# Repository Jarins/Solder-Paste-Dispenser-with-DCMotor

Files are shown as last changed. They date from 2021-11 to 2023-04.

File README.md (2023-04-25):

# 3D Printed Solder-Paste-Dispenser with DC motor
Motorized automatic solder paste dispenser. Easily printable on a 3D printer at home
+ **Thanks [kevarek](https://hackaday.io/Kevarek) for inspiration from this [project:](https://hackaday.io/project/169748-low-cost-solder-paste-dispenser)**
+ The idea came from this project, including some parts of the source code that were partially or completely reworked and many new ones added. 

## __Work-in-progress__ Latest version 2.21.11.3010

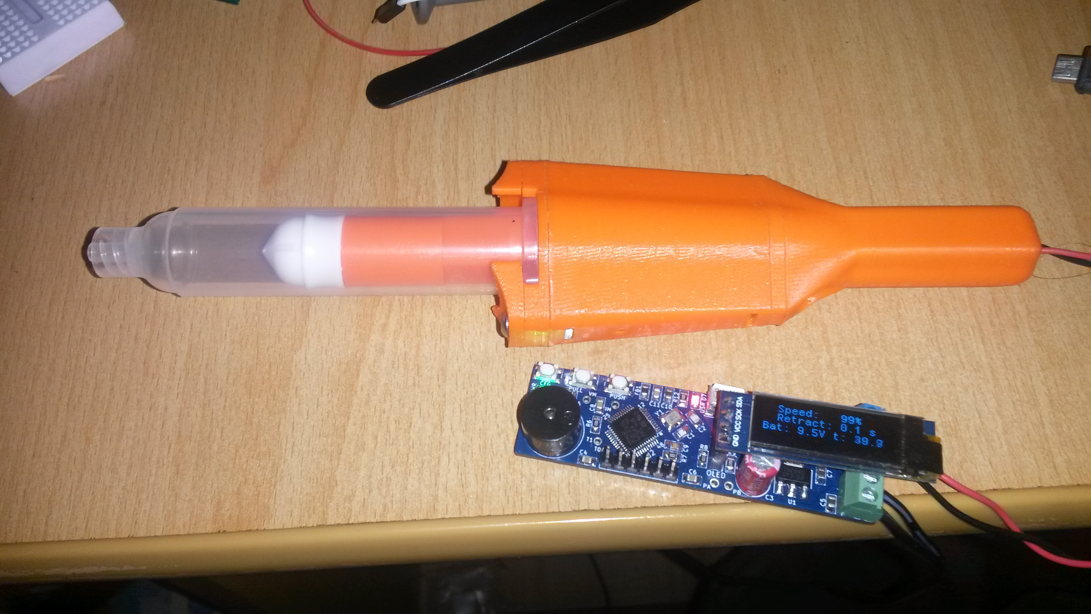
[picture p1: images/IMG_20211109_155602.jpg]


### Some differences:

+ Controled with 32bit processor STM32F103C8T6 ( original is STM32F030)
+ used output H-bridge for motor control [TB67H451FNG](https://www.aliexpress.com/item/1005001738294266.html?spm=a2g0s.9042311.0.0.27424c4dVMVyey). **No need cooling with during operation**.
+ 
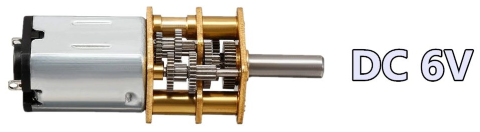
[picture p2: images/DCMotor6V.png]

+ [DC micromotor 6V / 60 rpm](https://www.aliexpress.com/item/33022320164.html?spm=a2g0s.9042311.0.0.266b4c4dmW3uVV) with gearbox without thread rod 


+ [Coupler](https://www.aliexpress.com/item/1005002015620915.html?spm=a2g0s.9042311.0.0.266b4c4dmW3uVV) 3/4mm to thread rod M4.
 
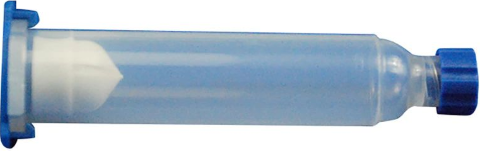
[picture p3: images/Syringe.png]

+ larger [syringe 10 ccm](https://www.aliexpress.com/item/10000092421369.html?spm=a2g0s.9042311.0.0.27424c4dw27aah)

+ **redesigned mechanism of operation and piston mounting and mainly redesigned Syringe mount, which can be removed and put on without disassembling the dispenser**

!! warning component links may be invalid over time !!

----------------------------------------------------------------------

+ [I2C OLED display 128x32](https://www.aliexpress.com/item/32879702750.html?spm=a2g0s.9042311.0.0.27424c4d1LUqwi) pixels for setting dispensing parameters and monitoring operating data
+ The supply voltage is 9V
+ The MicroUSB port is only used for 5V power supply when programming and debugging firmware to save battery. In this mode it is necessary to disconnect the 9V battery. The USB DM and DP pins are connected to the CPU, but the firmware does not respond to them. 
+ **Resistor R2** (in schematic) for measuring motor current is in the current version mounted with the value 0R, because the possibility of measuring this current is not used at the moment. When this value (0R) is used, the H-bridge turns off motor current monitoring.

#### PCB is designed by KiCAD software
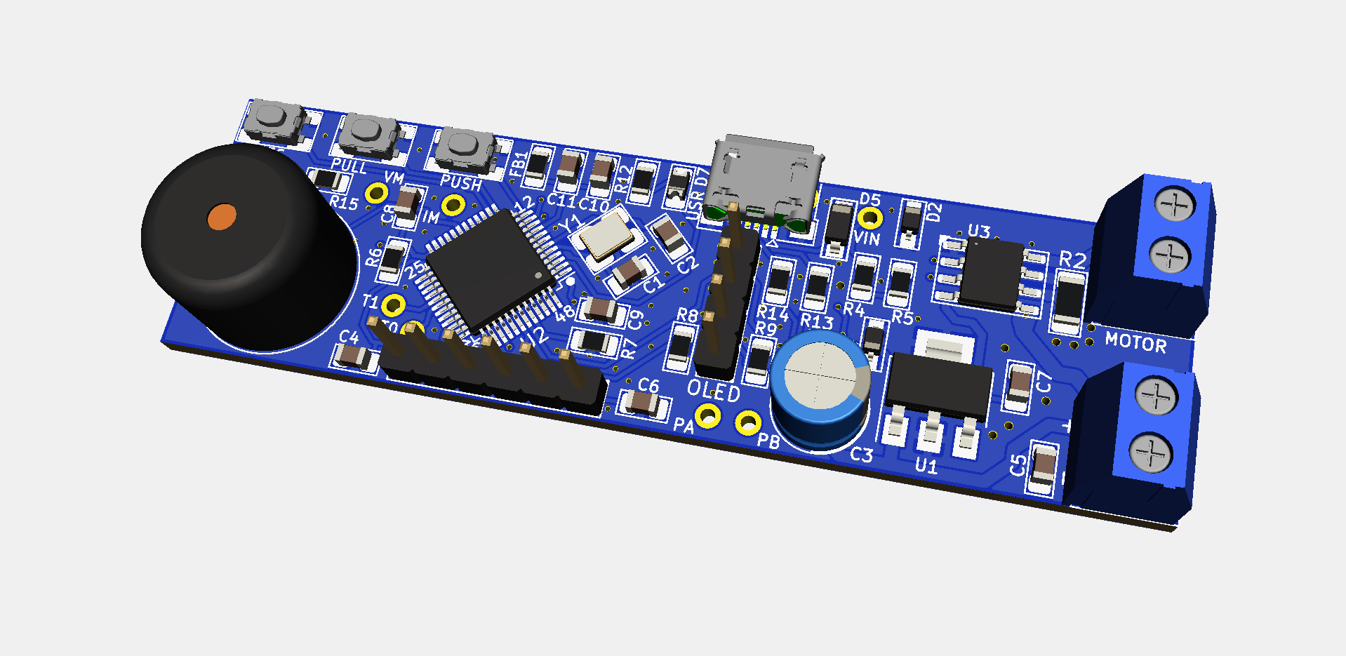
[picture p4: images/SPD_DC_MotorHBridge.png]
Pict2


+ Source code of Firmware is optimized for STM32CubeIDE and CubeMX software from ST Microelectronics.

+ Source code are easy aplicable to another IDE.

+ It would be a little more difficult to migrate to the Arduino IDE, but even that is partially possible - it has not been tested

+ CAD files are designed in SolidWorks, preview [here](https://grabcad.com/library/3d-printed-solder-paste-dispenser-1):

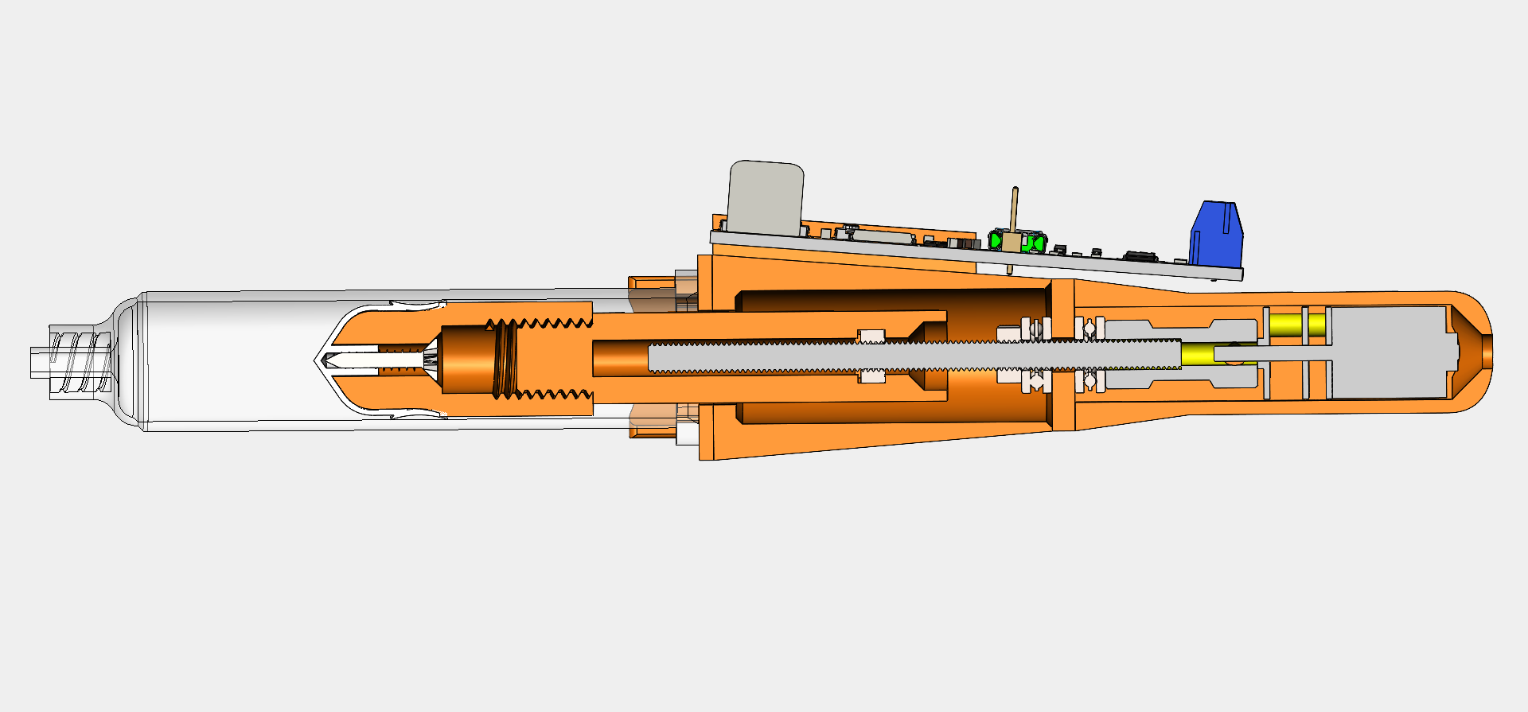
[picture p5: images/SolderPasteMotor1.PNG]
 

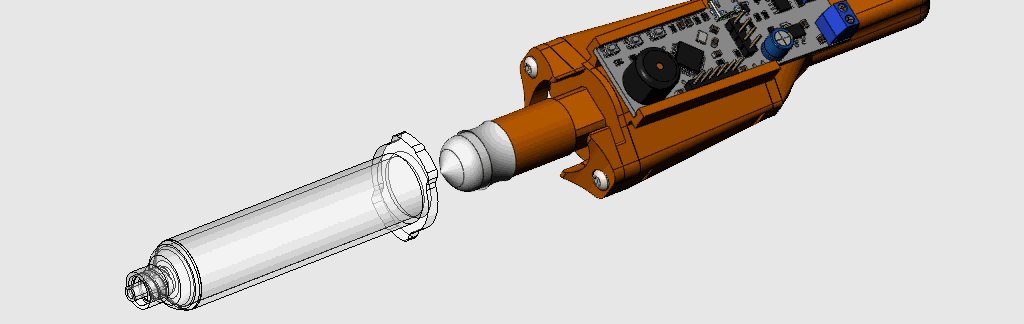
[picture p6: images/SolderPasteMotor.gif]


**Auto Extrusion cycle:**
+ PUSH button short switch ON -> Return from retract(retract duration time) -> Pulse for extrusion(pulse time) -> Retract(retract duration time)

**Manual Extrusion** 
+ PUSH button long switch ON(more as Retract duration time + Pulse time) -> extrusion until the PUSH button is switch OFF. This mode is used to insert a filled Syringe.

**Manual Retract**
+ PULL button switch ON -> retraction until the PULL button is switch OFF. This mode is using for remove and fill Syringe.
+
+ After selection, all parameters are immediately saved in the emulated EPROM (FLASH CPU).
+ Speed: 5, 10, 15 ...... 100% step by 5% 
+ Retract duration: 0(dissable), 100, 200 ...... 2500ms step by 100 milliseconds
+ Pulse after piston returned from retraction: 0(dissable), 100, 200 ..... 1500ms  step by 100 milliseconds 
+ Continuous measurement of battery voltage and CPU temperature
+ The firmware uses a non-blocking I2C DMA routine for the OLED display (this saves about 20 ms in the loop) **and Loop() no waiting to DMA complete as is usual in many of the examples given, which then makes the DMA a blocking wait routine**
+ In addition, non-blocking User Timers derived from SysTick interrupts are used, which do not stop the CPU while waiting for the Timer to run out. The number of these Timers is limited only by the CPU speed and the amount of allocated RAM) *more about this in* [*loop.c*](Software/CubeMX/Application/loop.c)

+ **Tasks**
+ [x] ***The continuation of the work consists in the completion of the control button mounted on the Syringe tube and the tuning of the SW for optimal paste dispensing. This is a game with engine on and off times and duty cycle of PWM wave***
+ [ ] Create a video with instructions for assembly and demonstration at work. Soon.
+ [ ] electronics attachment and power supply solution for the future possibility of 12V power supply from a 3D printer.
+ [ ] Next step is using this solder paste dispenser with a 3D printer. It may be necessary to use a stepping motor for dispensing instead. It has a better and more accurate dispensing control option. I have already finished the PCB for this variant with the DRV8825 controller and the NEMA14 stepper motor. 

UPDATE 11/22/2021:
- Syringe control button completed
- New version firmware 2.0. No blocked Dealy() in Loop() cycle
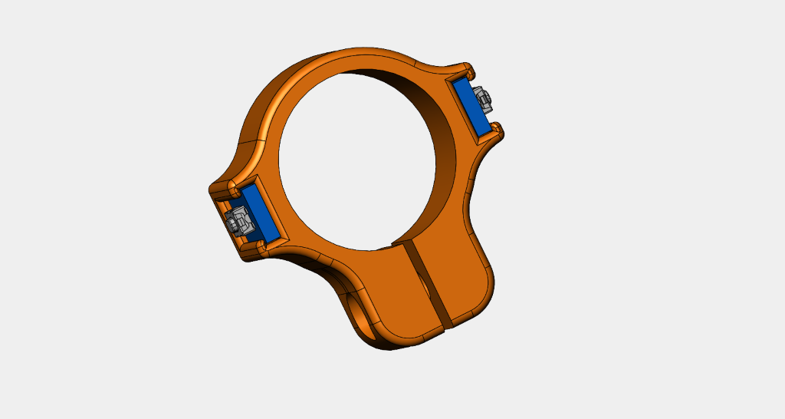
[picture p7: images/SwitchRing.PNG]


#### [Video Assembly and first testing](https://youtu.be/biS96wBTfaU) (redirect to YouTube) 
+ The first version of the printouts on my 3D printer
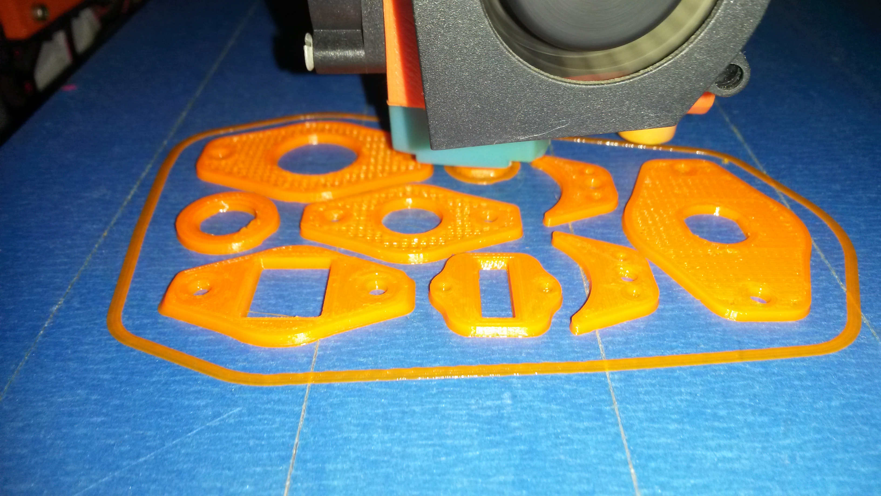
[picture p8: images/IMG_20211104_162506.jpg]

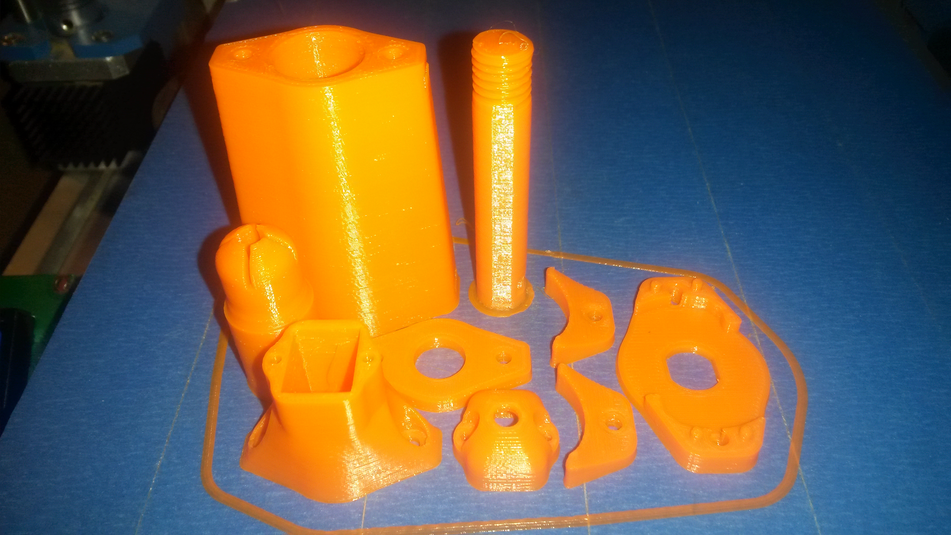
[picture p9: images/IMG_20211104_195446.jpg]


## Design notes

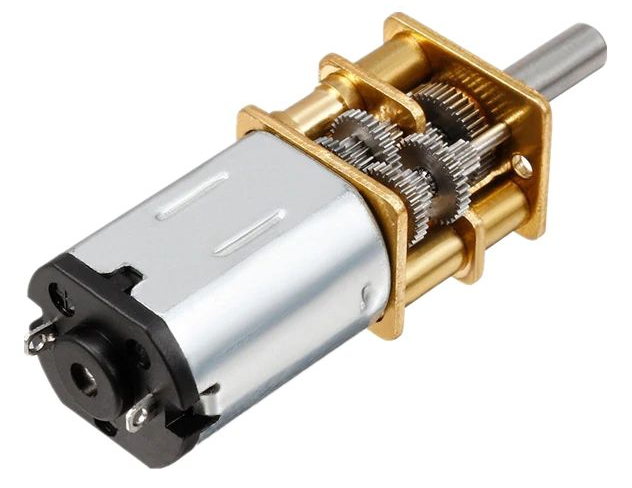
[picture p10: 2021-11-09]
images/DCMotor6V_1.png

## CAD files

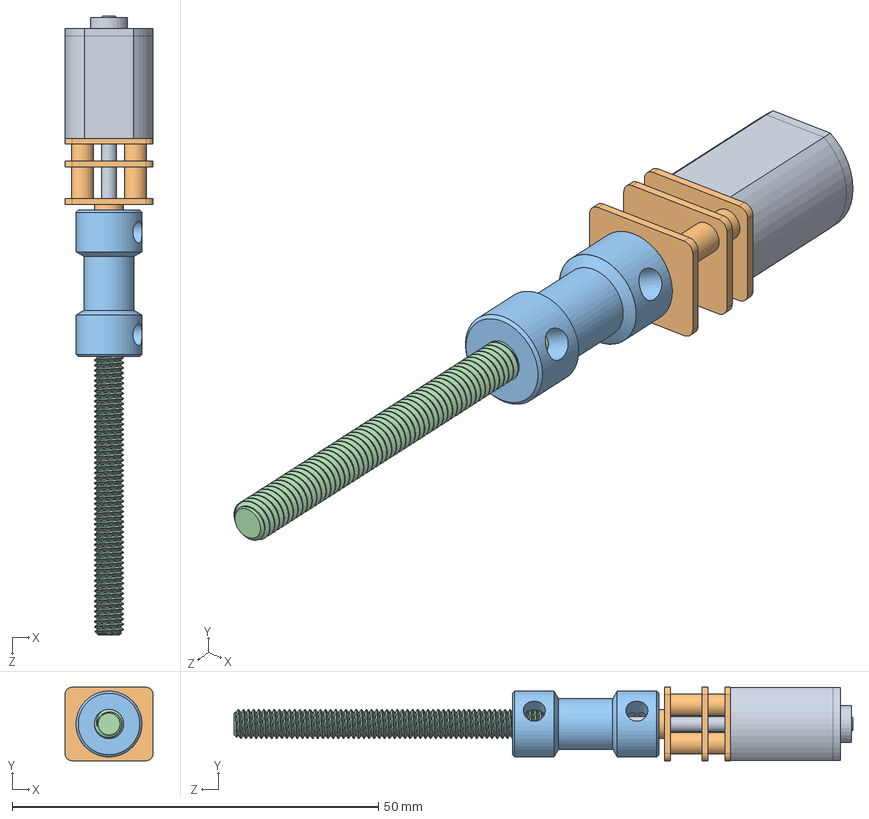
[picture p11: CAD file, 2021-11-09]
CAD/MotorGearBox.SLDASM
12.1 x 10.0 x 84.5 mm
Motor
GearBox
Coupling
ThreadRod

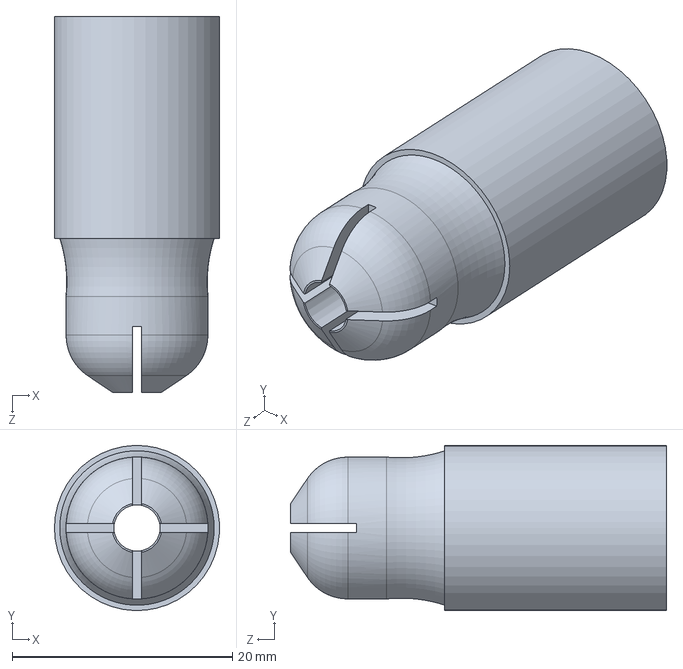
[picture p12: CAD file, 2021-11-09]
CAD/PistonHolder.SLDPRT
15.0 x 15.0 x 34.2 mm

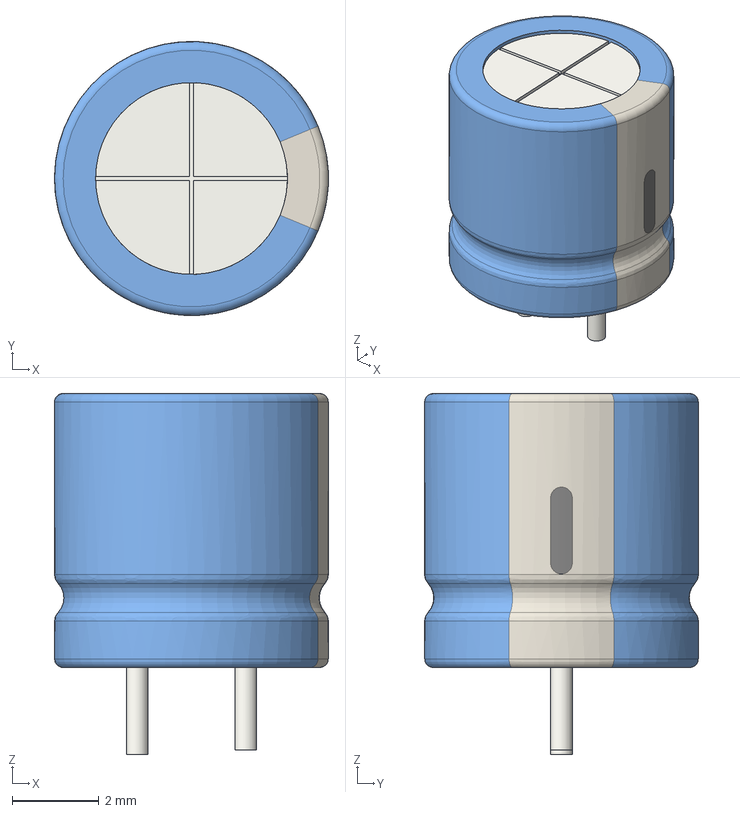
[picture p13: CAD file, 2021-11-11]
Hardware/shapes3D/CP_Radial_D6.3mm_P2.50mm.step
6.30 x 6.30 x 8.30 mm

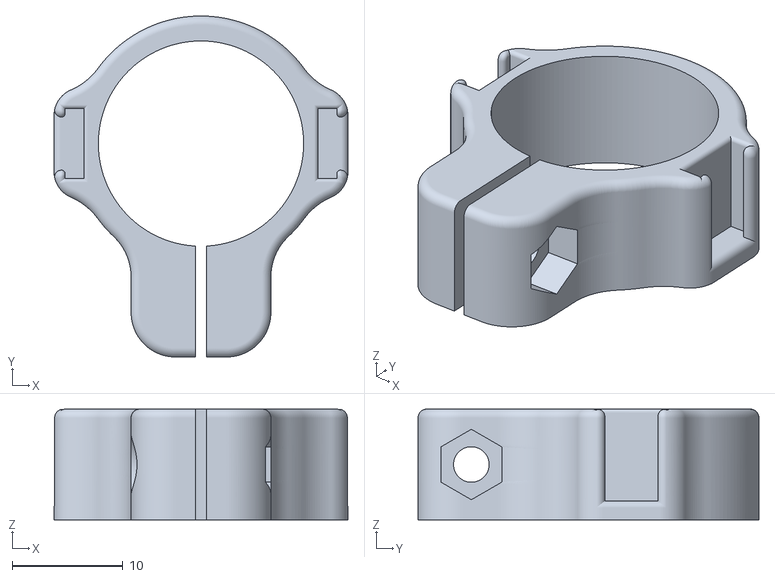
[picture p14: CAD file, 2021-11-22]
STL/SwitchRing.STL
26.5 x 30.7 x 10.0

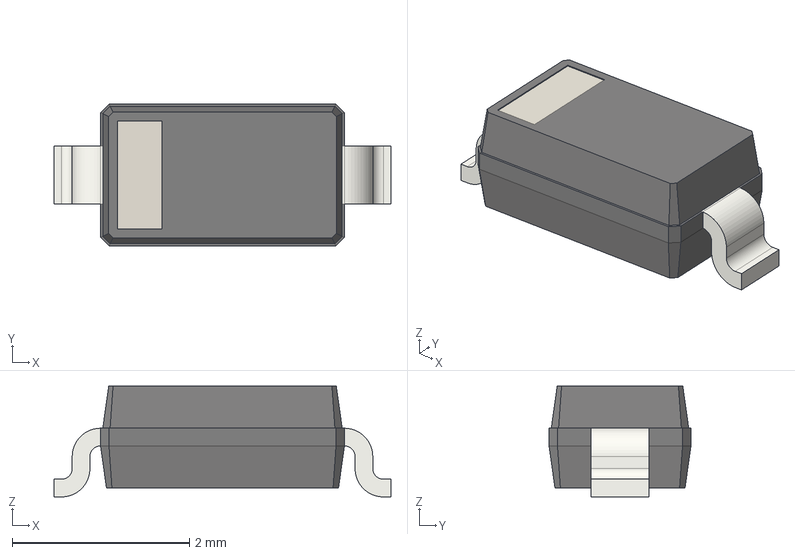
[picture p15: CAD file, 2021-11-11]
Hardware/shapes3D/D_SOD-123.step
3.80 x 1.60 x 1.25 mm

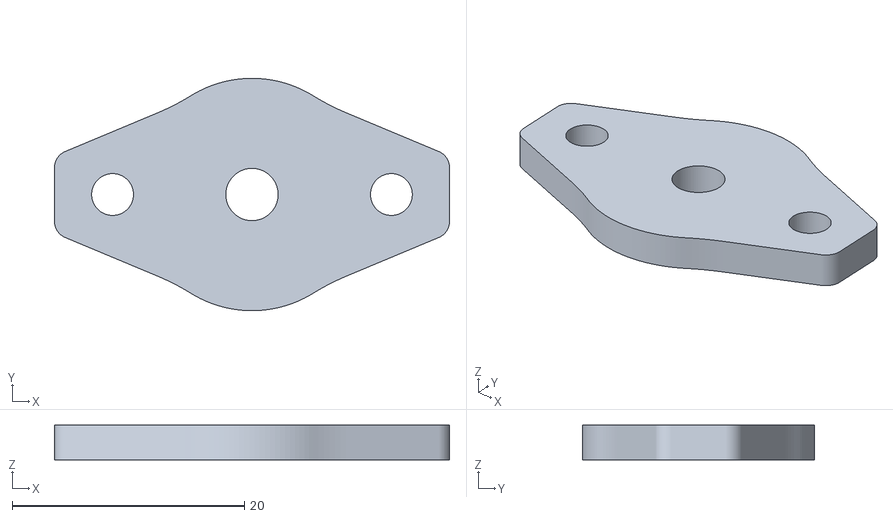
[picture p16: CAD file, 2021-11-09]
STL/ShaftMountFlatAxial.STL
34.0 x 20.0 x 3.00

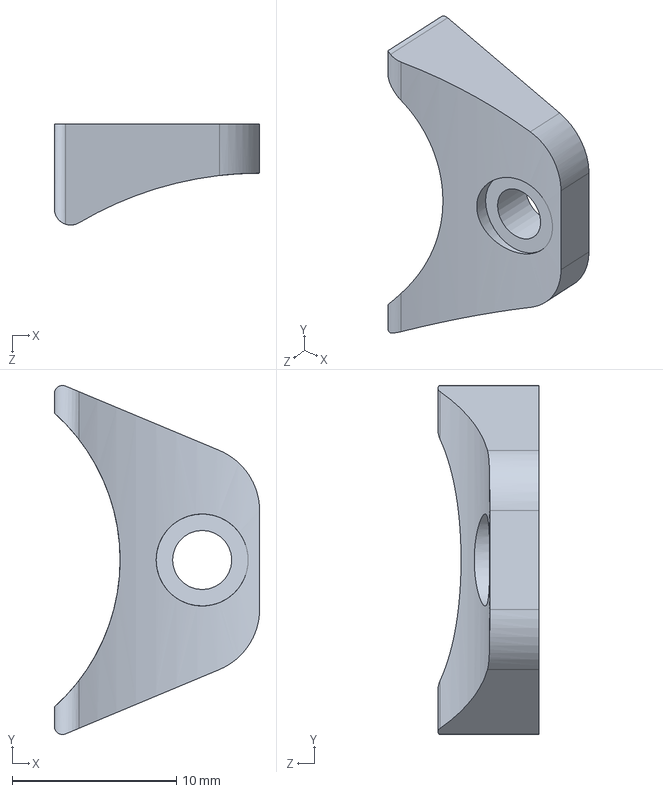
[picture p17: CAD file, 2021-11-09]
CAD/SyringeFixtureTube.SLDPRT
12.5 x 21.2 x 6.15 mm

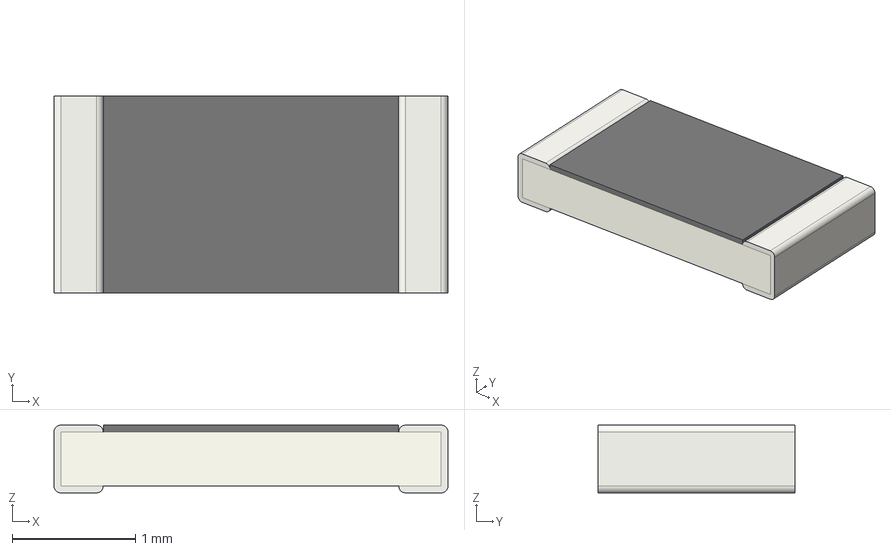
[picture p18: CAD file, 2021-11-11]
Hardware/shapes3D/R_1206_3216Metric.step
3.20 x 1.60 x 0.55 mm

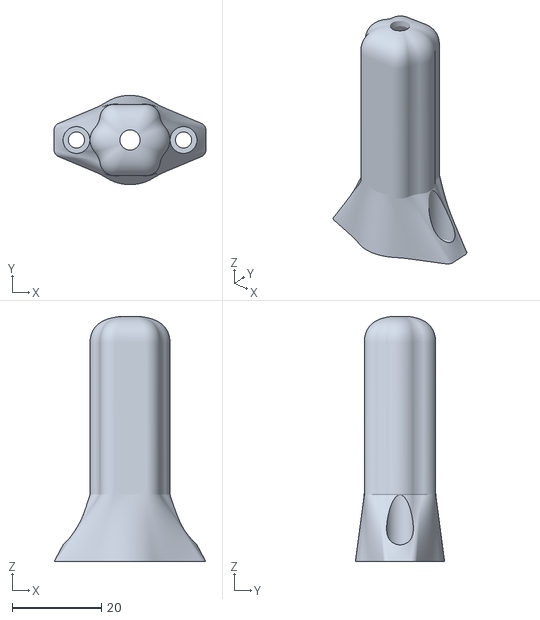
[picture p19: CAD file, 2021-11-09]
STL/TopCoverAxial.STL
34.0 x 20.0 x 54.9

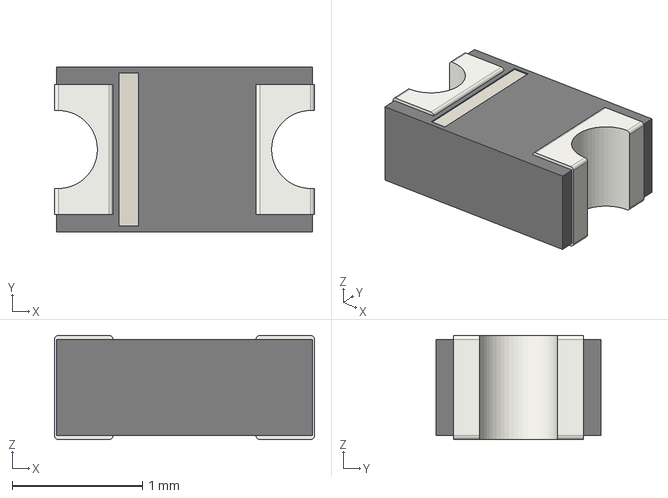
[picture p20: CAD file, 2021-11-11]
Hardware/shapes3D/D_0805_2012Metric.step
2.00 x 1.27 x 0.8 mm

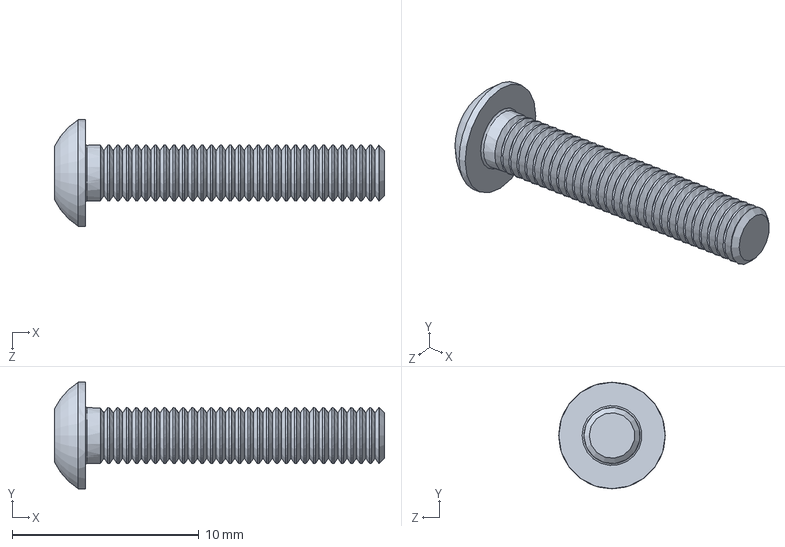
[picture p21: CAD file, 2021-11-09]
CAD/SroubM3x16pulkulata.SLDPRT
17.7 x 5.70 x 5.70 mm

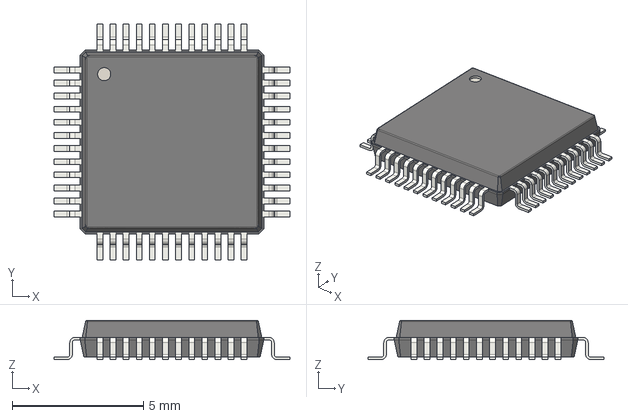
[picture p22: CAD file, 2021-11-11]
Hardware/shapes3D/LQFP-48_7x7mm_P0.5mm.step
9.00 x 9.00 x 1.50 mm

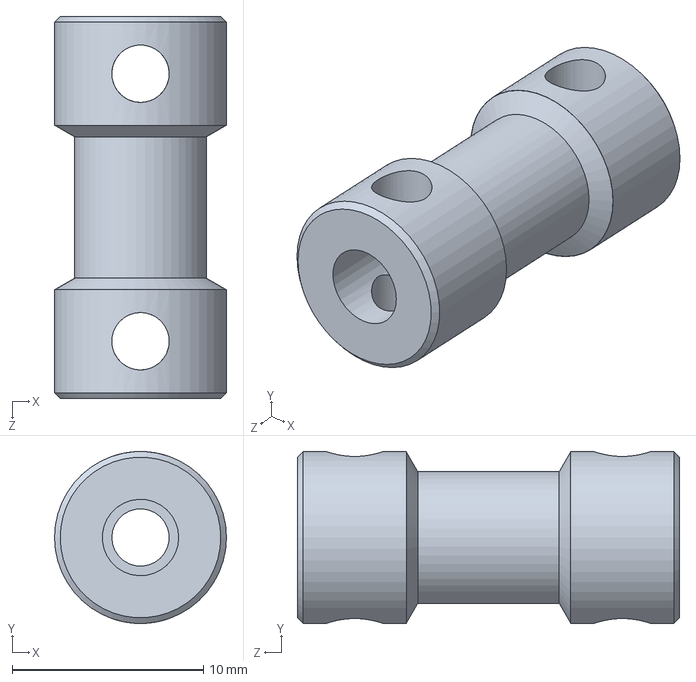
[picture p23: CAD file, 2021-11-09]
CAD/Coupling.SLDPRT
9.00 x 9.00 x 20.0 mm

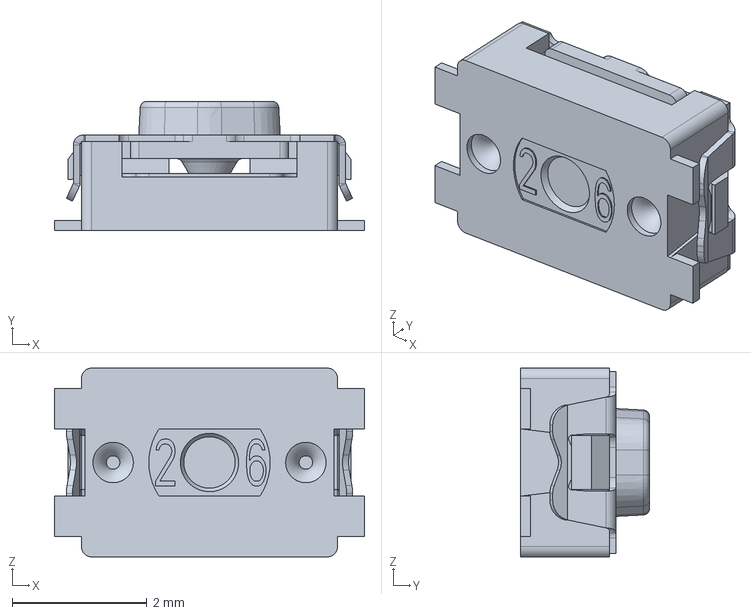
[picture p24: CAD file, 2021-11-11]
Hardware/shapes3D/KMR231NGLFS.stp
4.60 x 1.92 x 2.80 mm

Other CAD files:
CAD/TopCover.SLDPRT
CAD/Matice M3 Ctverec.SLDPRT
Hardware/shapes3D/C_0805_2012Metric.step
CAD/GearBox.SLDPRT
CAD/AxialniLozisko_F4-10_10x4x4.SLDPRT
CAD/Matice M4.SLDPRT
CAD/Motor.SLDPRT
CAD/Piston.SLDPRT
CAD/ShaftCover.SLDPRT
CAD/ShaftMountFlat.SLDPRT
CAD/Syringe.SLDPRT
CAD/SyringeFixtureLockFlat.SLDPRT
CAD/SyringePiston.SLDPRT
CAD/ThreadRod.SLDPRT
Hardware/shapes3D/Buzzer_12x9.5RM7.6.step
Hardware/shapes3D/Crystal_SMD_SeikoEpson_TSX3225-4Pin_3.2x2.5mm_HandSoldering.step
Hardware/shapes3D/D_SOD-323.step
Hardware/shapes3D/HSOP-8-1EP_3.9x4.9mm_P1.27mm_EP2.41x3.1mm.step
Hardware/shapes3D/PinHeader_1x04_P2.54mm_Vertical.step
Hardware/shapes3D/PinHeader_1x06_P2.54mm_Vertical.step
Hardware/shapes3D/R_0805_2012Metric.step
Hardware/shapes3D/SOT-223.step
Hardware/shapes3D/Screw Terminal Block 3.5mm Blue 2-way.step
STL/Piston.STL
STL/PistonHolder.STL
STL/ShaftCover.STL
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

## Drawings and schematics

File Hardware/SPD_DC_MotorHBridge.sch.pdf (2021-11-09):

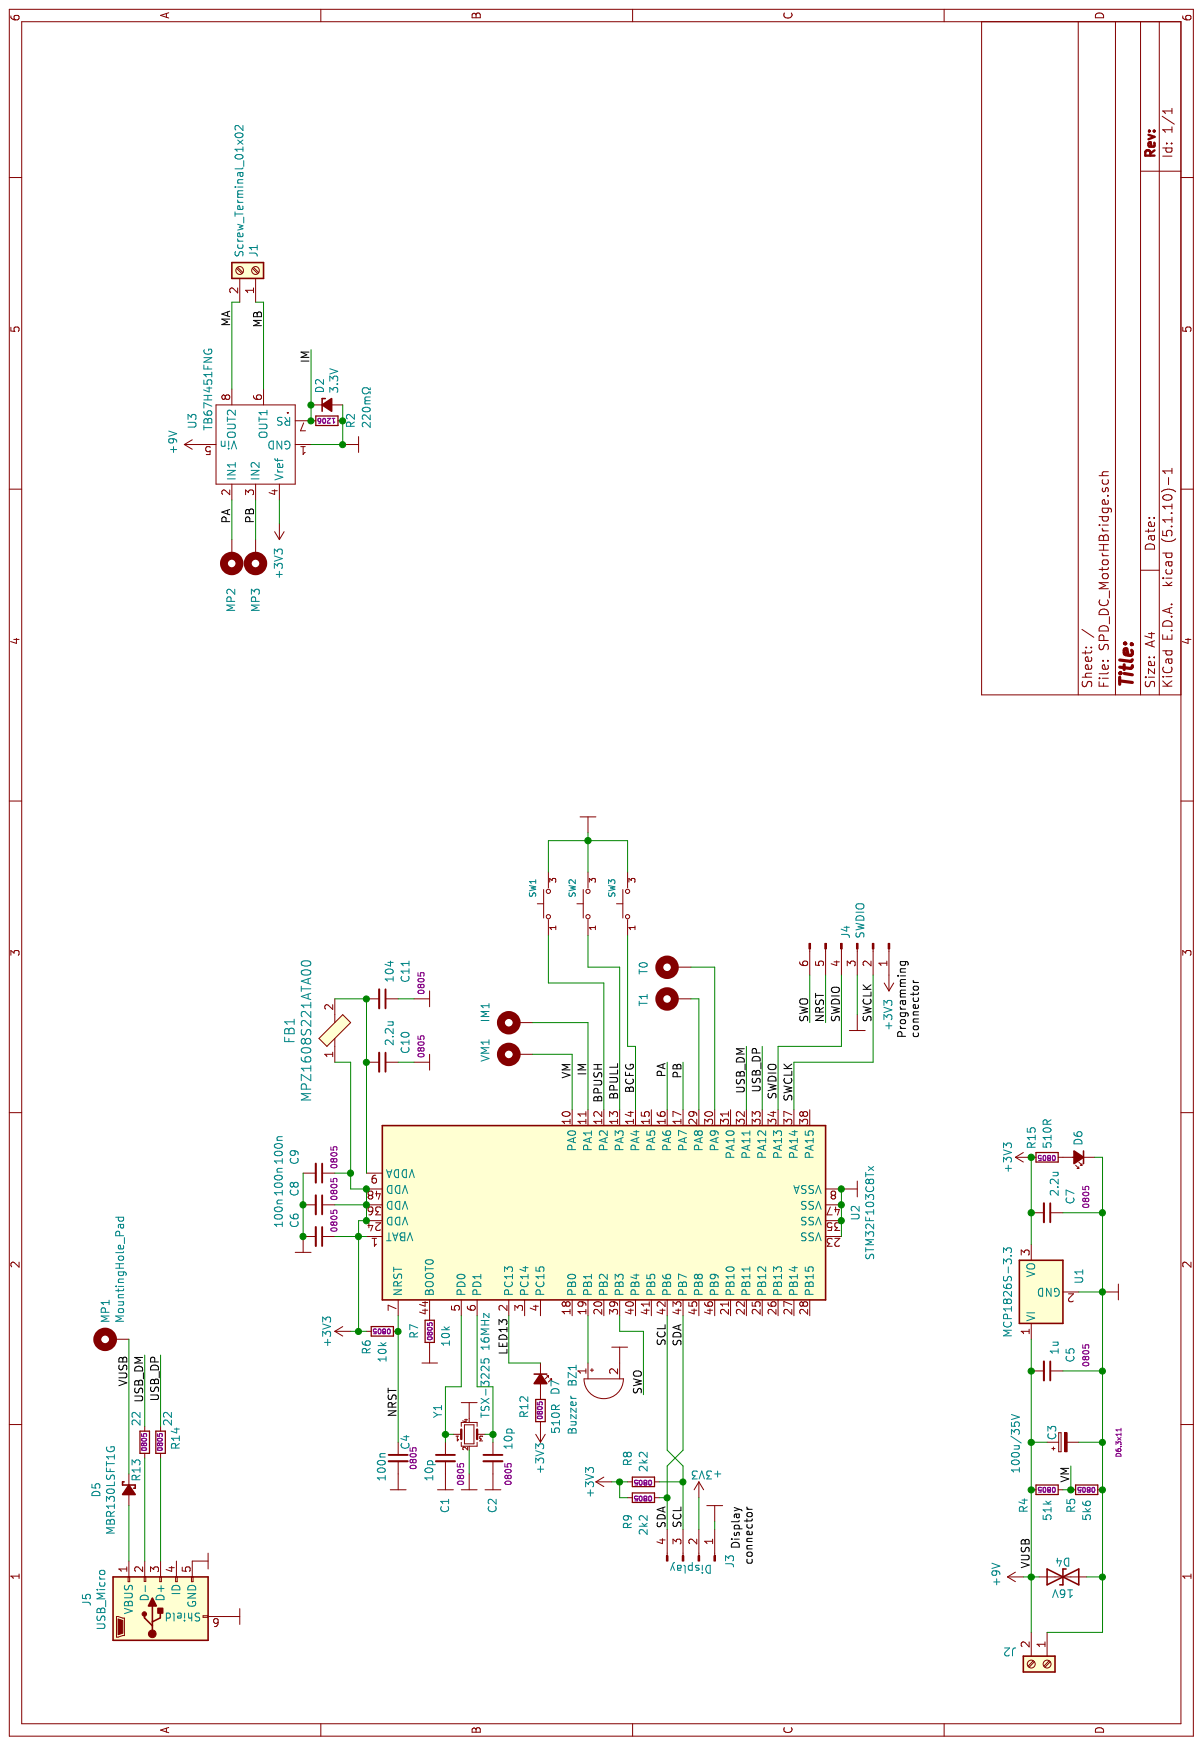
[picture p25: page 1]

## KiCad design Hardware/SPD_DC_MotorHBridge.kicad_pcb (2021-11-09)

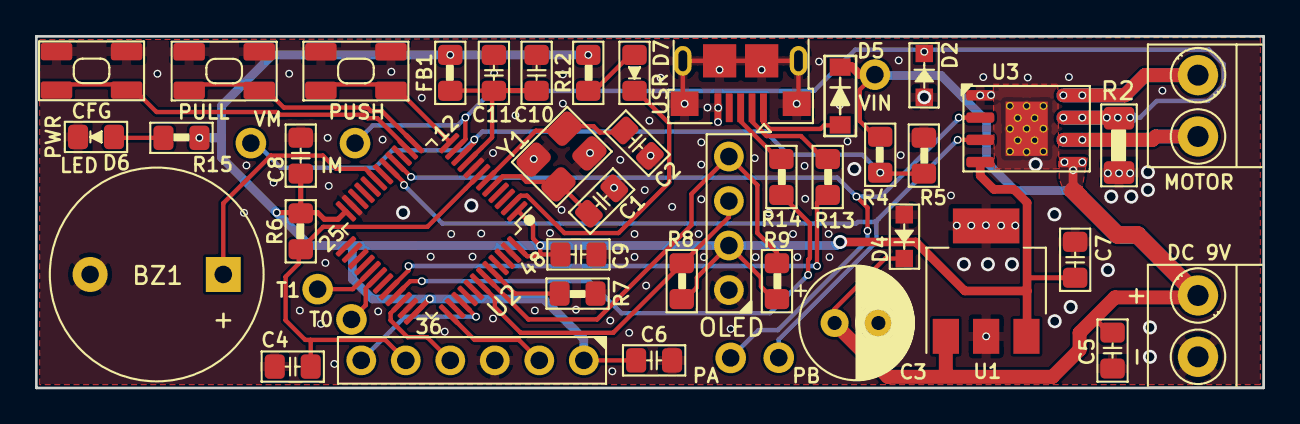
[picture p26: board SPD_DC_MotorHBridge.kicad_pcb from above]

Board: 2 copper layers, 70.0 x 20.1 mm, 48 parts (0 on the bottom side), 33 nets.

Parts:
BZ1: Buzzer; Buzzer_12x9.5RM7.6
C1, C2: 10p; C_0805_2012Metric_Pad1.15x1.40mm_HandSolder
C3: 100u/35V; CP_Radial_D6.3mm_P2.50mm
C4, C6, C8, C9: 100n; C_0805_2012Metric_Pad1.15x1.40mm_HandSolder
C5: 1u; C_0805_2012Metric_Pad1.15x1.40mm_HandSolder
C7, C10: 2.2u; C_0805_2012Metric_Pad1.15x1.40mm_HandSolder
C11: 104; C_0805_2012Metric_Pad1.15x1.40mm_HandSolder
D2: 3.3V; D_SOD-323_HandSoldering
D4: 16V; D_SOD-323_HandSoldering
D5: MBR130LSFT1G; D_SOD-123
D6, D7: LED_Small_ALT; SMD_Dioda_0805
FB1: MPZ1608S221ATA00; R_0805_2012Metric_Pad1.15x1.40mm_HandSolder
IM1: MountingHole_Pad; Hole_Pad
J1, J2: Screw_Terminal_01x02; TerminalBlock_1x02_P3.50mm_Horizontal
J3: Display; PinHeader_1x04_P2.54mm_Vertical
J4: SWDIO; PinHeader_1x06_P2.54mm_Vertical
J5: USB_Micro; USB_Micro-B_Amphenol_10118193-0001LF_Horizontal
MP1, MP2, MP3: MountingHole_Pad; Hole_Pad
R2: 0; R_1206_3216Metric_Pad1.30x1.75mm_HandSolder
R4: 51k; R_0805_2012Metric_Pad1.15x1.40mm_HandSolder
R5: 5k6; R_0805_2012Metric_Pad1.15x1.40mm_HandSolder
R6, R7: 10k; R_0805_2012Metric_Pad1.15x1.40mm_HandSolder
R8, R9: 2k2; R_0805_2012Metric_Pad1.15x1.40mm_HandSolder
R12, R15: 510R; R_0805_2012Metric_Pad1.15x1.40mm_HandSolder
R13, R14: 22; R_0805_2012Metric_Pad1.15x1.40mm_HandSolder
SW1, SW2, SW3: TactSwichWhite; KEY-SMD-4.2X3.2X2.5-White
T0, T1: MountingHole_Pad; Hole_Pad
U1: MCP1826S-3.3; SOT-223-3_TabPin2
U2: STM32F103C8Tx; LQFP-48_7x7mm_P0.5mm
U3: TB67H451FNG; HSOP-8-1EP_3.9x4.9mm_P1.27mm_EP2.41x3.1mm_ThermalVias
VM1: MountingHole_Pad; Hole_Pad
Y1: TSX-3225 16MHz; Crystal_SMD_TSX3225-4Pin_3.2x2.5mm_HandSoldering

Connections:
+3V3: C6.1, C7.2, C8.1, C9.1, FB1.1, J3.2, J4.1, R6.1, R8.1, R9.1, R12.2, R15.1, U1.3, U2.1, U2.24, U2.36, U2.48, U3.4
+9V: C3.1, C5.2, D4.1, D5.1, J2.2, MP1.1, R4.1, U1.1, U3.5
/BCFG: SW3.1, SW3.2, U2.14
/BPULL: SW2.1, SW2.2, U2.13
/BPUSH: SW1.1, SW1.2, U2.12
/IM: D2.1, IM1.1, R2.1, U2.11, U3.7
/LED13: D7.1, U2.2
/MA: J1.2, U3.8
/MB: J1.1, U3.6
/NRST: C4.1, J4.5, R6.2, U2.7
/PA: MP2.1, U2.16, U3.2
/PB: MP3.1, U2.17, U3.3
/SCL: J3.3, R8.2, U2.42
/SDA: J3.4, R9.2, U2.43
/SWCLK: J4.2, U2.37
/SWDIO: J4.4, U2.34
/SWO: J4.6, U2.39
/USB_DM: R13.1, U2.32
/USB_DP: R14.1, U2.33
/VM: R4.2, R5.1, U2.10, VM1.1
GND: BZ1.2, C1.2, C2.2, C3.2, C4.2, C5.1, C6.2, C7.1, C8.2, C9.2, C10.1, C11.1, D2.2, D4.2, D6.1, J2.1, J3.1, J4.3, J5.5, J5.6, R2.2, R5.2, R7.2, SW1.3, SW1.4, SW2.3, SW2.4, SW3.3, SW3.4, U1.2, U2.8, U2.23, U2.35, U2.47, U3.1, Y1.2, Y1.4
unnamed: BZ1.1, U2.19
unnamed: C1.1, U2.5, Y1.1
unnamed: C2.1, U2.6, Y1.3
unnamed: C10.2, C11.2, FB1.2, U2.9
unnamed: D5.2, J5.1
unnamed: D6.2, R15.2
unnamed: D7.2, R12.1
unnamed: J5.2, R13.2
unnamed: J5.3, R14.2
unnamed: R7.1, U2.44
unnamed: T0.1, U2.30
unnamed: T1.1, U2.29

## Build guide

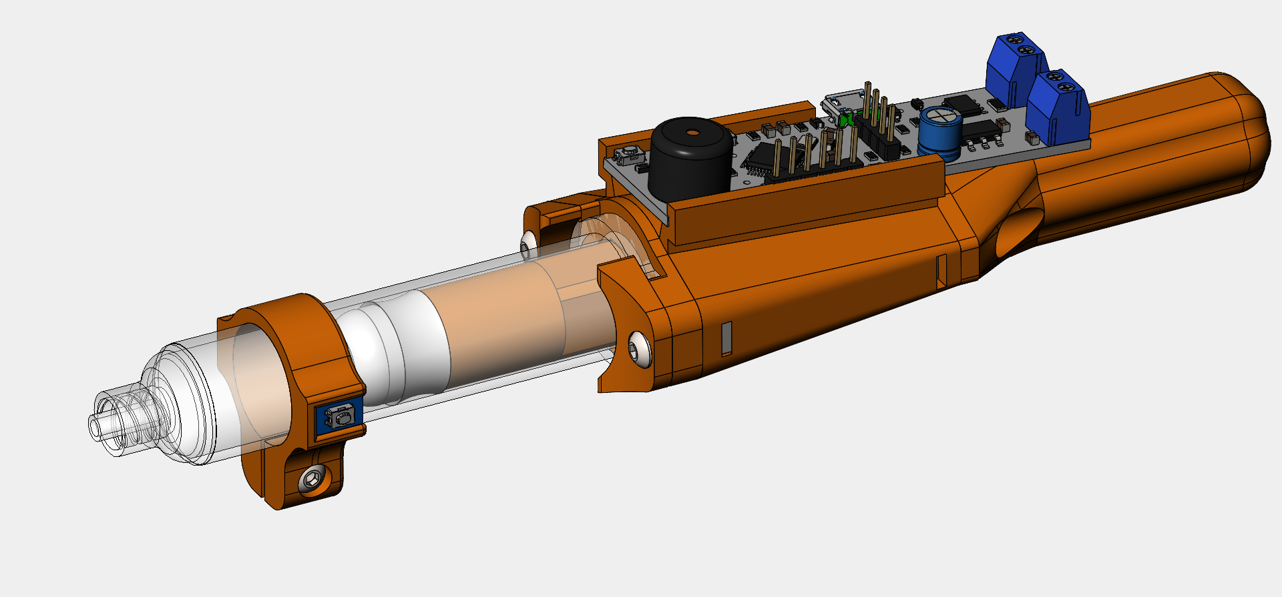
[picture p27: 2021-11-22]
images/SolderPasteMotor.PNG

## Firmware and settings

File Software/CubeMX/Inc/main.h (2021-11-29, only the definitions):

#define LED_Pin GPIO_PIN_13
#define LED_GPIO_Port GPIOC
#define VM_Pin GPIO_PIN_0
#define VM_GPIO_Port GPIOA
#define IM_Pin GPIO_PIN_1
#define IM_GPIO_Port GPIOA
#define BPUSH_Pin GPIO_PIN_2
#define BPUSH_GPIO_Port GPIOA
#define BPUSH_EXTI_IRQn EXTI2_IRQn
#define BPULL_Pin GPIO_PIN_3
#define BPULL_GPIO_Port GPIOA
#define BPULL_EXTI_IRQn EXTI3_IRQn
#define BCFG_Pin GPIO_PIN_4
#define BCFG_GPIO_Port GPIOA
#define BCFG_EXTI_IRQn EXTI4_IRQn
#define SYSCLK_Pin GPIO_PIN_5
#define SYSCLK_GPIO_Port GPIOA
#define PB_Pin GPIO_PIN_6
#define PB_GPIO_Port GPIOA
#define PA_Pin GPIO_PIN_7
#define PA_GPIO_Port GPIOA
#define BEEP_Pin GPIO_PIN_1
#define BEEP_GPIO_Port GPIOB
#define TEST1_Pin GPIO_PIN_8
#define TEST1_GPIO_Port GPIOA
#define TEST_Pin GPIO_PIN_9
#define TEST_GPIO_Port GPIOA
#define SWDIO_Pin GPIO_PIN_13
#define SWDIO_GPIO_Port GPIOA
#define SWCLK_Pin GPIO_PIN_14
#define SWCLK_GPIO_Port GPIOA
#define SWO_Pin GPIO_PIN_3
#define SWO_GPIO_Port GPIOB
#define I2C_SCL_Pin GPIO_PIN_6
#define I2C_SCL_GPIO_Port GPIOB
#define I2C_SDA_Pin GPIO_PIN_7
#define I2C_SDA_GPIO_Port GPIOB

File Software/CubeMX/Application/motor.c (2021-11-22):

/*
 * motor.c
 *
 *  Created on: Dec 8, 2019
 *      Author: Standa
 */

#include "motor.h"
#include "utility.h"
#include "tim.h"
#include "main.h"


#define MO_SPEED_MIN	80//100
#define MO_SPEED_MAX	800//999

volatile int16_t Speed;


void mo_Init(void){

}


void mo_SetSpeed(int16_t speed){

	Speed = speed;

	HAL_TIM_Base_Stop(&htim3);
	HAL_TIM_PWM_Stop(&htim3,TIM_CHANNEL_1);  //PA_Pin Stop pwm
	HAL_TIM_PWM_Stop(&htim3,TIM_CHANNEL_2);  //PB_Pin Stop pwm

	HAL_GPIO_WritePin(PA_GPIO_Port,PA_Pin,GPIO_PIN_RESET);   // Stop motor
	HAL_GPIO_WritePin(PB_GPIO_Port,PB_Pin,GPIO_PIN_RESET);

	if(speed > 0){
		UT_SATURATE(speed, MO_SPEED_MIN, MO_SPEED_MAX);
		HAL_GPIO_WritePin(PA_GPIO_Port,PA_Pin,GPIO_PIN_RESET);
		HAL_GPIO_WritePin(PB_GPIO_Port,PB_Pin,GPIO_PIN_SET);

		__HAL_TIM_SET_COMPARE(&htim3,TIM_CHANNEL_1,speed); //Set motor speed% voltage
		HAL_TIM_PWM_Start(&htim3,TIM_CHANNEL_1);  //PA_Pin Start pwm motor speed% duty cycle
		HAL_TIM_Base_Start(&htim3);
	}
	else if(speed < 0){
		speed *= -1;
		UT_SATURATE(speed, MO_SPEED_MIN, MO_SPEED_MAX);
		HAL_GPIO_WritePin(PA_GPIO_Port,PA_Pin,GPIO_PIN_SET);
		HAL_GPIO_WritePin(PB_GPIO_Port,PB_Pin,GPIO_PIN_RESET);

		__HAL_TIM_SET_COMPARE(&htim3,TIM_CHANNEL_2,speed); //Set motor speed% voltage
		HAL_TIM_PWM_Start(&htim3,TIM_CHANNEL_2);  //PB_Pin Start pwm motor speed% duty cycle
		HAL_TIM_Base_Start(&htim3);
	}
}

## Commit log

2021-11-10 Create SolderPasteMotor1.PNG
    Files
2021-11-11 PCB Library
2021-11-22 Version 2.0
    [SwitchRing.STL]

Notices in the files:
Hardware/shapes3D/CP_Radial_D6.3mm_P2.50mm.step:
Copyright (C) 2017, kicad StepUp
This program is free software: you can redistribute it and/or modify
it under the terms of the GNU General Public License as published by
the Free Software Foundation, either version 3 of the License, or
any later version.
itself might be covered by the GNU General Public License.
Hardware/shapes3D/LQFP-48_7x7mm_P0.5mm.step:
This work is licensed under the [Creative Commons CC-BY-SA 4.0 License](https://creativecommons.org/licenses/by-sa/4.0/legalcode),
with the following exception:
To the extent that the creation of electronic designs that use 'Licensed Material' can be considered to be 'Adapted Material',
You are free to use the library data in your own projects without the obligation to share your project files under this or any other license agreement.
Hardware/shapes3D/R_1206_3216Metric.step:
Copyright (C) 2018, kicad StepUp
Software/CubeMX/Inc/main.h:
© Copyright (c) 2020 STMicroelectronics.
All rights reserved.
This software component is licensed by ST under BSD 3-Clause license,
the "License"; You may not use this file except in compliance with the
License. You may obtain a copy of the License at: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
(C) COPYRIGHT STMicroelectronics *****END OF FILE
